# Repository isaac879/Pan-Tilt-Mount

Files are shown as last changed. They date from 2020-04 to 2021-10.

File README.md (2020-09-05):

# 3-Axis Slider
A stepper motor driven, 3D printed and Arduino Nano controlled 3-axis slider.

Project Overview:
This is the 3-axis slider I designed for my DSLR Canon EOS 250D (EOS Rebel SL3). I designed it for video motion control, time-lapses and panoramic shots.

Here is a quick overview of the components and how the project works. There is an Arduino Nano as the brain controlling everything and monitoring the inputs. The three Nima 17 stepper motors are controlled by TMC2208 stepper driver boards. When combining the stepper motor’s step angle, the microstepping mode of the driver boards and the gear ratios of the pan and tilt axis you get a precision of 0.0133° and 0.0369° respectively (Stepper motors move 1.8° per full step, microstepping divides this by 16, the pan axis has a gear ratio of 144:17 and the tilt has a ratio of 64:21). 
The slider carriage moves using a 36 tooth timing pulley with a 2GT timing belt on 2040 V-slot aluminium extrusion. This gives the slider has a positional precision of approximately 0.0225mm.

In 16th microstepping mode, axis speeds are limited to about 20 degrees per second for the pan, 15 degrees per second for the tilt and 20mm per second for the slider. This limit is due to the software/microcontroller speed which is only able to produce ~4000 step pulses per second for the 3 stepper motors. In half stepping mode speeds about eight times higher should be possible depending on acceleration profiles and camera weight.

The pan, tilt and slider are almost completely silent in 16th microstepping mode. In half stepping mode when moving at full speed the noise is audible.

The maximum weight I have tested it with is just over 1kg. This was with my Canon EOS 250D with the heaviest lens I have (Canon EF-S 18-135mm f/3.5-5.6) and a Rode Video Mic Pro+. This worked without any issues although some shaking does occur when rapidly changing directions.

There are Hall effect sensors and magnets embedded in the pan, tilt and slider axis to allow the stepper motors to home and zero themselves. The circuit can be powered by a 12V DC input or 3 cell LiPo battery for portability. With a 1000mAh battery the 3-axis slider can operate for abount one hour. The Arduino will monitors the battery level and print it out. The Arduino can also trigger the camera’s shutter using an NPN transistor and 2.5mm 3 pole jack. 

Communicating with the Arduino is simply over a serial connection provided by the USB or JDY-31 serial pass-through Bluetooth module.

The 3-Axis slider project video/demo: https://youtu.be/1FfB7cLkUyQ

Some picture, videos and development updates are available on my Instagram: https://www.instagram.com/isaac879/

The CAD STL and STEP files are available here: https://www.thingiverse.com/thing:4547074

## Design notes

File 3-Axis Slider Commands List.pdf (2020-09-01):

isaac879

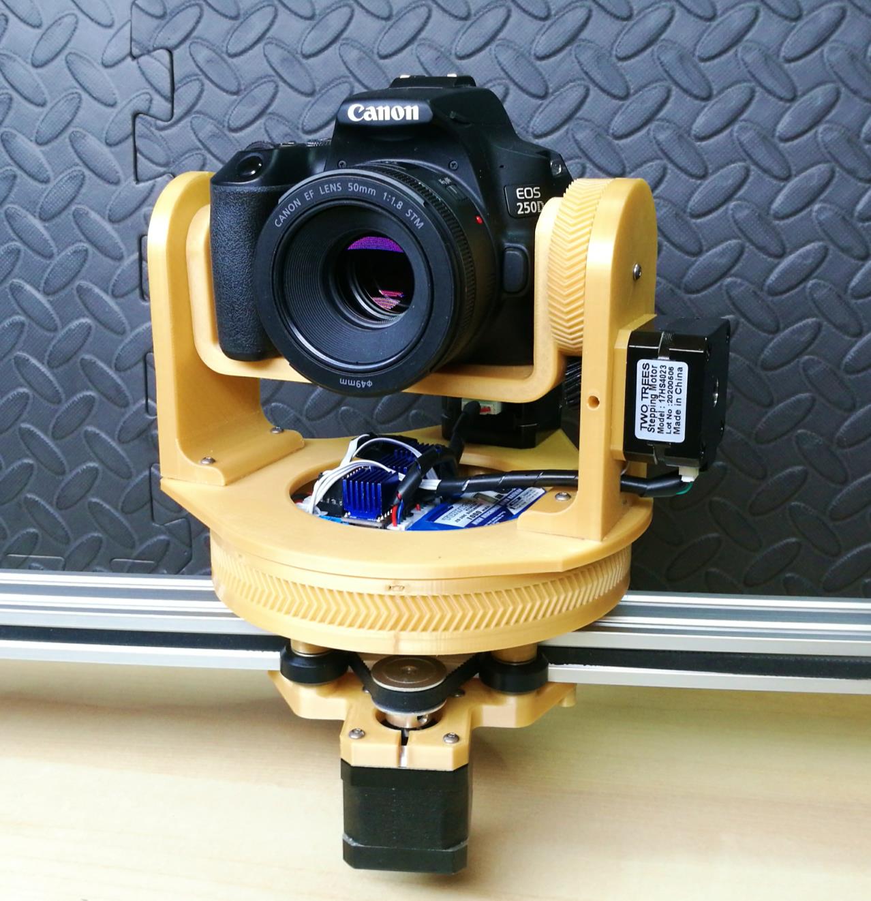
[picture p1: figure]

3-Axis Slider | Page 1 of 3

# 3-Axis Slider Commands List

Function | Command Character | Input Range
Report status | R | N/A
Set Step Mode | m | 2, 4, 8, 16
Pan x degrees | p | float
Tilt x degrees | t | float
Toggle enable motors | e | N/a
Set maximum pan speed (deg/s) | s | float
Set maximum tilt speed (deg/s) | S | float
Invert pan direction | i | bool
Invert tilt direction | I | bool
Set pan hall effect offset (deg) | o | float
Set tilt hall effect offset (deg) | O | float
Set homing mode (0: No homing, 1: Slider, 2: Pan & Tilt, 3: All axis) | H | 0-3
Trigger camera shutter | c | N/A
Auto home the axis | A | N/A
Execute moves array | ; | 1-32767
Add current position to moves array | # | N/A
Step forward a position in the moves array | > | N/A
Step backward a position in the moves array | < | N/A
Move to the first position in the moves array | [ | N/A
Move to the last position in the moves array | ] | N/A
Edit the current position in the moves array with current position | E | N/A
Add a delay in the moves array (ms) | d | 0-32767
Edit a delay at the current position in the moves array (ms) | D | 0-32767
Clear all position in the moves array | C | N/A
Save the current settings in EEPROM | U | N/A
Start a panoramic-lapse | L | N/A
Set angle between pictures (deg) | b | float
Set delay between pictures (ms) | B | 0-32767
Start a time lapse with x pictures | l | 1-32767
Move slider x mm | x | float
Invert slider direction | j | bool
Set maximum slider speed (mm/s) | X | float
Auto Home the slider axis | Z | N/A
Calculate the intercept of the first 2 keyframes | T | N/A
Move between the 2 keyframes, keeping pointed at the intercept | @ | 0-32767
Toggle axis acceleration on/off | a | N/A
Pan acceleration increment delay (µs) | q | 0-32767
Tilt acceleration increment delay (µs) | Q | 0-32767
Slider acceleration increment delay (µs) | w | 0-32767
Scale the speed of all keyframed movements | W | float

To use a function listed in the table you need to send the appropriate command over the serial connection to the Arduino. The serial connection can be over USB or Bluetooth as they both work the same. You can simply use the serial monitor provided in the Arduino IDE or one of many Android apps (I use Arduino Bluetooth controller by Giumig Apps). Bluetooth modules commonly have a default baud rate of 9600 which will need to be changed to 57600 to avoid any timing issues with the code.

Examples:
To get the pan tilt mount to print out its current status just send “R” (without quotes). To set the step mode to 16th stepping move send: “m16” (without quotes).
To move the pan axis -22.5 degrees send: “p-22.5” (without quotes).

Important:
When the code is first uploaded the EEPROM values will not have been properly set and will result in unusable values. You will need to set appropriate values then save them to the EEPROM (by sending he command character U). A restart may then be required.
To see the current setting and stored EEPROM values send the command character R. The screenshots below show the settings and stored values before and after setting appropriate EEPROM values.

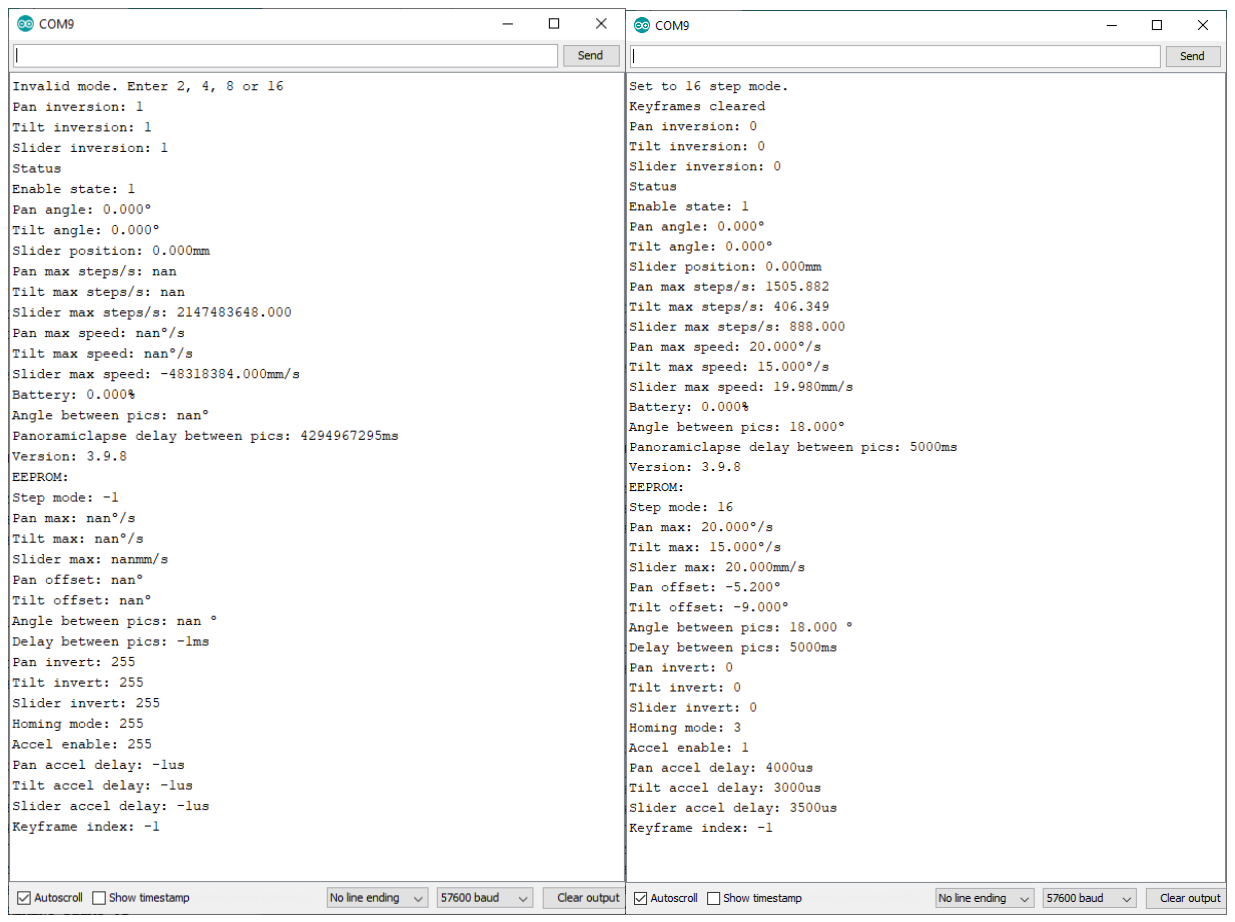
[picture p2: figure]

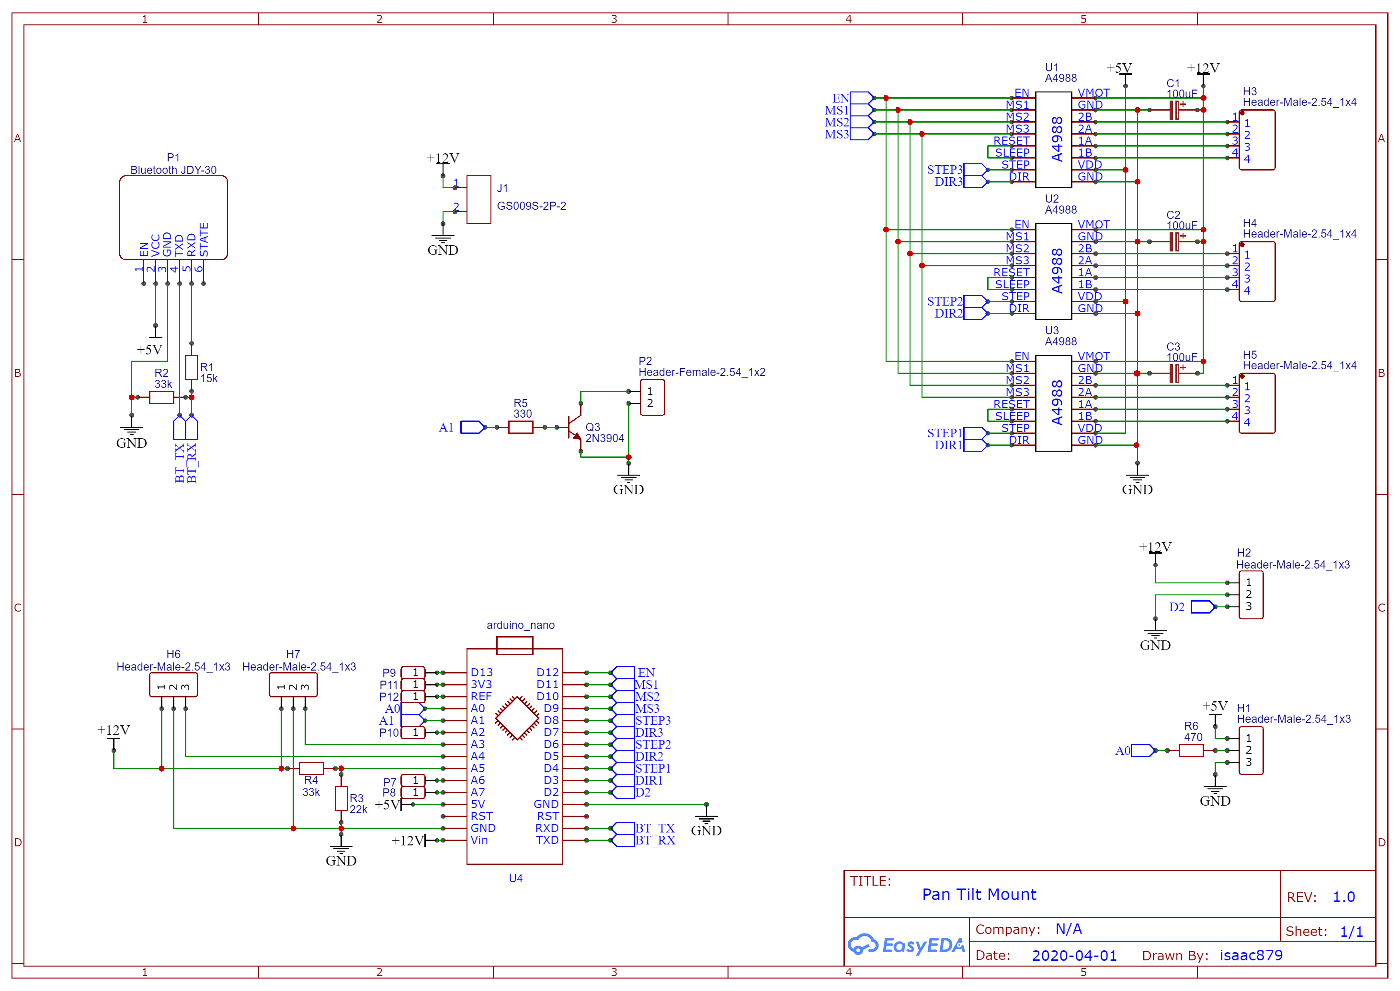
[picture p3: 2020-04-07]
Schematic_Pan Tilt Camera Mount_Sheet_1_20200401234411.png

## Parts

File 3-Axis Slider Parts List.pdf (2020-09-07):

isaac879

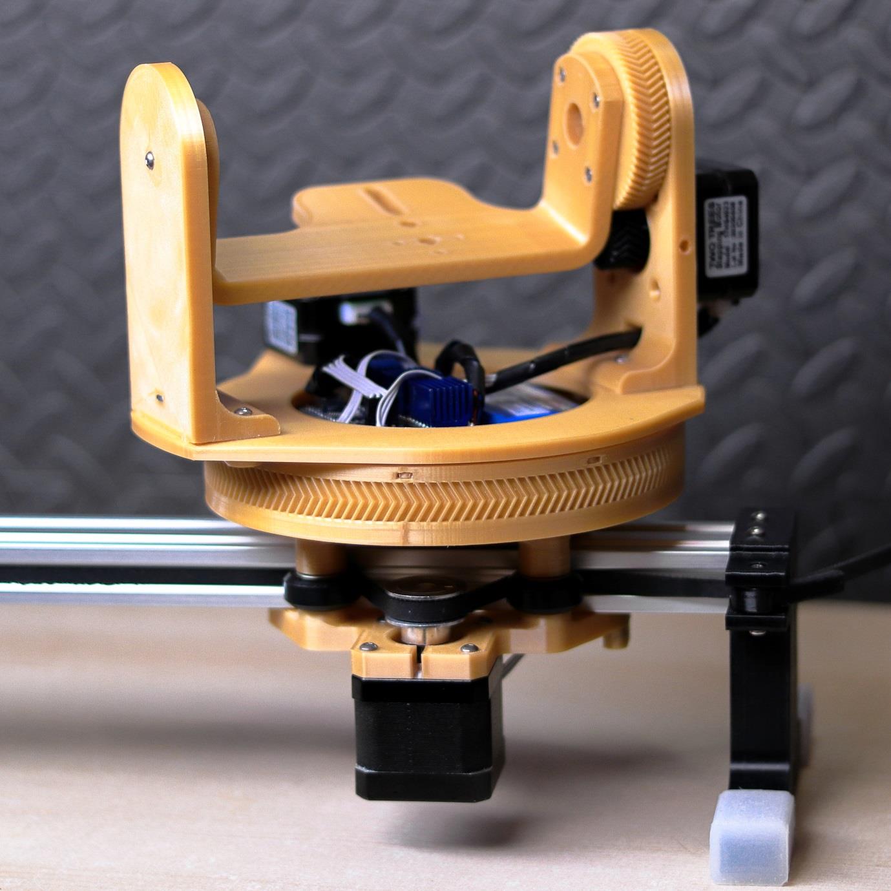
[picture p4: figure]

Linear Slider | Page 1 of 3

# 3-Axis Slider Parts List

3-Axis Slider Parts | Quantity
Nema 17 42 x 42 x 40mm Stepper Motor | 1
Nema 17 42 x 42 x 23mm Stepper Motor | 2
TMC2208 Stepper Motor Driver | 3
Arduino Nano | 1
JDY-31 Bluetooth Module (Alternatively HC-05, HC-06 or JDY-30) | 1
A3144 Hall Effect Sensor | 3
6.4mm diameter x 1.7mm Neodymium Magnets | 2
3.2mm diameter x 1.7mm Neodymium Magnets | 4
2N3904 NPN Transistor | 1
330Ω Resistor | 1
470Ω Resistor | 1
15kΩ Resistor | 1
22kΩ Resistor | 1
33kΩ Resistor | 2
100µF Electrolytic Capacitor | 3
2 Pin Plug-In Screw Terminal Block Connector 5.08mm Pitch (for power) | 1
6 Pin Female Header Connector 2.54mm (for Bluetooth module) | 1
15 Pin Female Header Connector 2.54mm (for Arduino Nano) | 2
15 Pin Male Header Connector 2.54mm (for Arduino Nano) | 2
8 Pin Female Header Connector 2.54mm (for Stepper drivers) | 6
8 Pin Male Header Connector 2.54mm (for Stepper drivers) | 6
XH2.54 4 Pin Terminal Socket Header (for Stepper motors) | 3
XH2.54 4 Pin Terminal Socket Plug (for Stepper motors) | 3
XH2.54 3 Pin Terminal Socket Header (for Hall Effect) | 3
XH2.54 3 Pin Terminal Socket Plug (for Hall Effect) | 3
XH2.54 2 Pin Terminal Socket Header (for camera shutter trigger) | 1
XH2.54 2 Pin Terminal Socket Plug (for camera shutter trigger) | 1
2.5mm 3 pole Jack Male (for camera trigger) | 1
11.1V 3S LiPo Battery or 12V DC Power Source and connector to screw terminal | 1
Pan Tilt Mount PCB | 1
Solder Wire
Cyanoacrylate or Hot Glue (for magnets and Hall Effect sensor) Wire (for Stepper motors, Hall sensors, Bluetooth module)
M3 Hexagonal Nyloc Nut | 16
M3 Square Nut | 10
M3 Button Head Hex Bolt 40mm | 4
M3 Button Head Hex Bolt 20mm | 3
M3 Button Head Hex Bolt 16mm | 10
M3 Button Head Hex Bolt 12mm | 14
M3 Button Head Hex Bolt 8mm | 5
M3 Button Head Hex Bolt 6mm | 5
M3 Button Head Hex Bolt 3.5mm | 1
Camera Mounting Bolt | 1
M3 T-Nut for Aluminium Extrusion Profile | 4

Screw 2mm Outer Thread Diameter, 6mm Long | 3
2GT Timing Belt | 1
2GT Timing Pulley 36 Teeth | 1
V-Slot 2040 Aluminium Extrusion | 1
F623ZZ Flange Bushing Ball Bearings 3 x 10 x 4mm | 6
V-Slot Pulley Wheels with Bearings (24 x 16 x 10.2mm) | 4
3D Printed Parts
127 x 146.05 x 12.7mm INA CSXU050-2RS Bearing Or 3D printable bearing parts 1-3 and 28 x 6mm balls (BB pellets) | 1
21 Tooth Herringbone Gear | 1
64 Tooth Herringbone Gear | 1
17 Tooth Herringbone Gear | 1
144 Tooth Herringbone Gear Base Mount | 1
Tilt U-Mount | 1
Idle Side Bearing Mount | 1
Gear Side Bearing Mount | 1
Idle Side Support | 1
Gear Side Support | 1
Pan Mount | 1
Pan Mount Bearing Clamp | 1
Base Mount Bearing Clip Ring | 1
2040 hall clamp | 1
2040 slider carriage top | 1
2040 slider carriage bottom | 1
2040 belt clamp side 1 | 1
2040 belt clamp side 2 | 1
2040 support leg (Optional)
Belt clamp lever | 2
3mm to 5mm wheel bearing spacer centred | 4
5mm to 8mm shaft spacer (for timing pulley if it has a 8mm bore) | 1

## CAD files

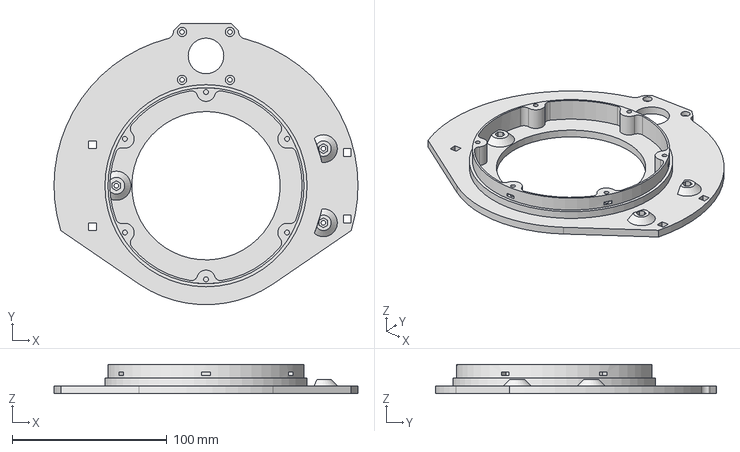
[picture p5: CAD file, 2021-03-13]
3-Axis Slider CAD STEP Exports/Pan Mount.stp
196.7 x 181.9 x 18.8 mm

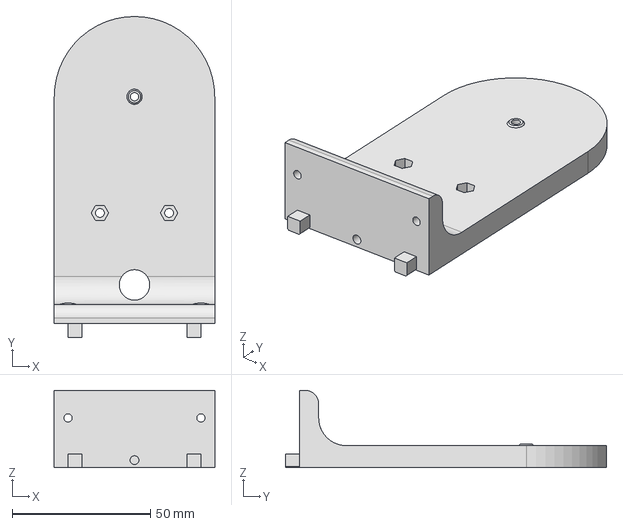
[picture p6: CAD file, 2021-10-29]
LP-E6 Battery Mount/Idle Side Support.stp
58.0 x 116.0 x 28.0 mm

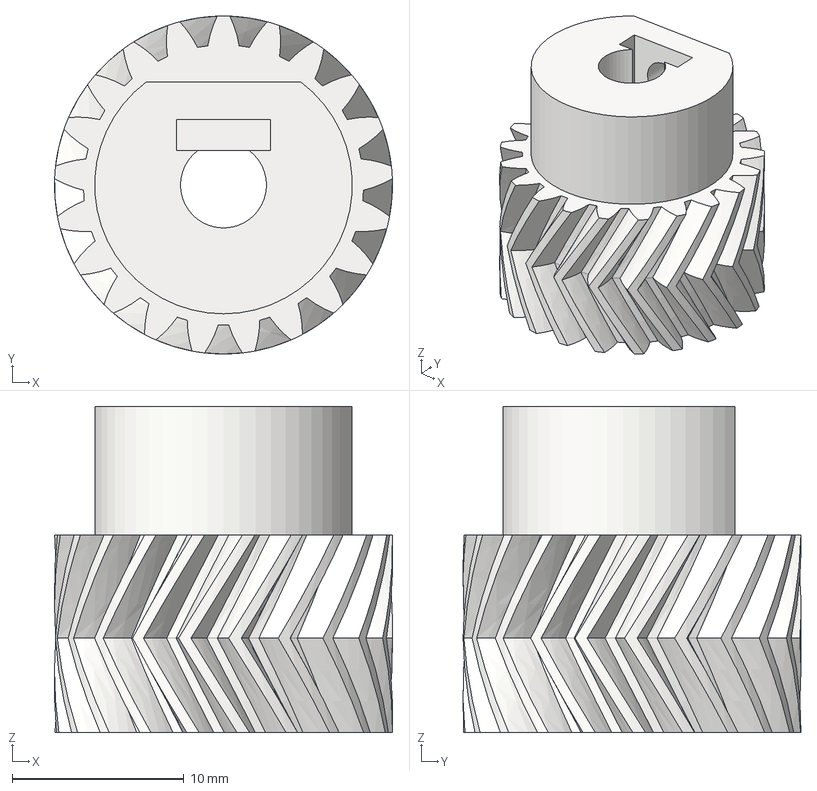
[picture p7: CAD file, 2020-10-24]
3-Axis Slider CAD STEP Exports/21 Tooth Herringbone Gear.stp
19.7 x 19.7 x 19.0 mm

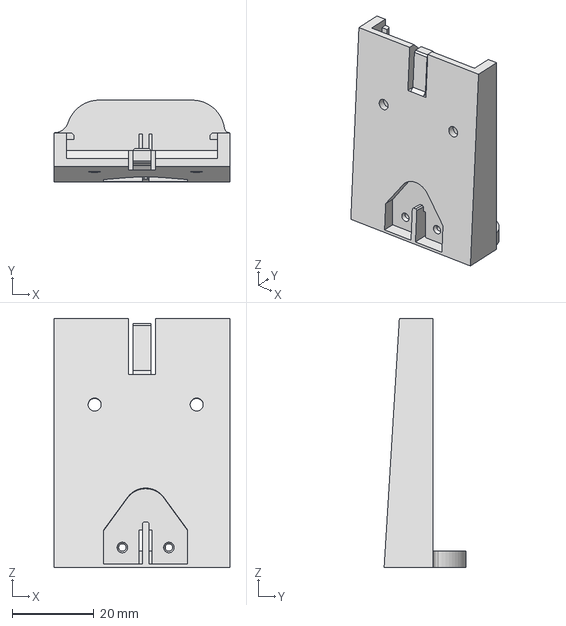
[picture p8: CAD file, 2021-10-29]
LP-E6 Battery Mount/LP-E6 Battery Holder Mount.stp
43.0 x 20.0 x 61.0 mm

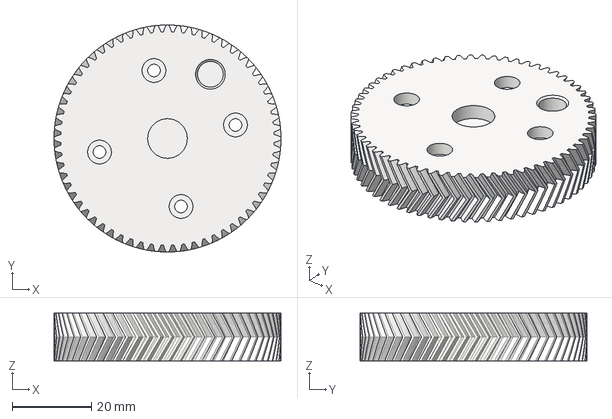
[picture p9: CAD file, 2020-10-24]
3-Axis Slider CAD STEP Exports/64 Tooth Herringbone Gear.stp
57.3 x 57.3 x 12.0 mm

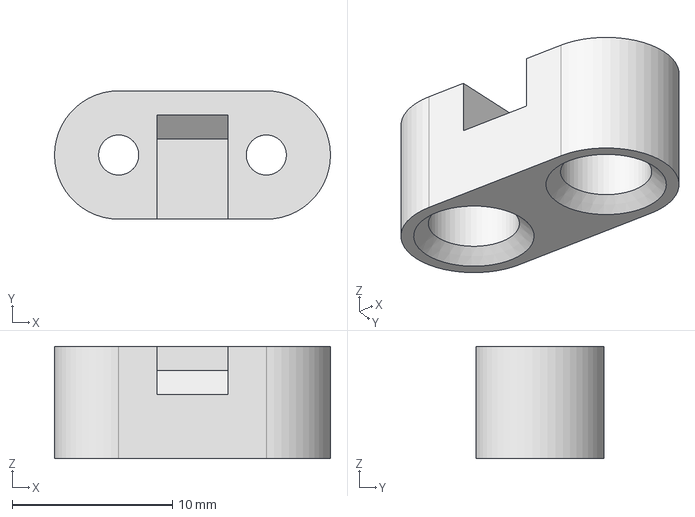
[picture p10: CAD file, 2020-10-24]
3-Axis Slider CAD STEP Exports/2040 hall clamp.stp
17.2 x 8.00 x 7.00 mm

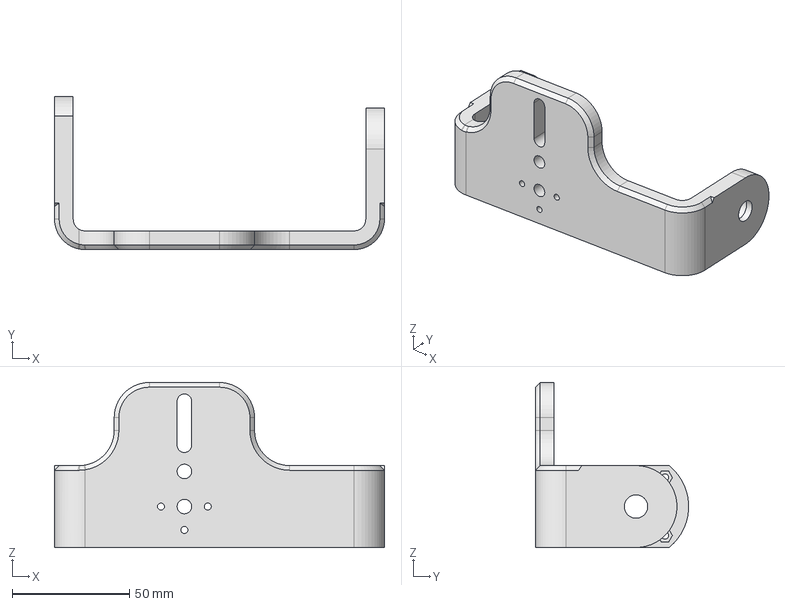
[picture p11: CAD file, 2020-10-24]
3-Axis Slider CAD STEP Exports/Tilt U-Mount.stp
141.0 x 65.5 x 70.5 mm

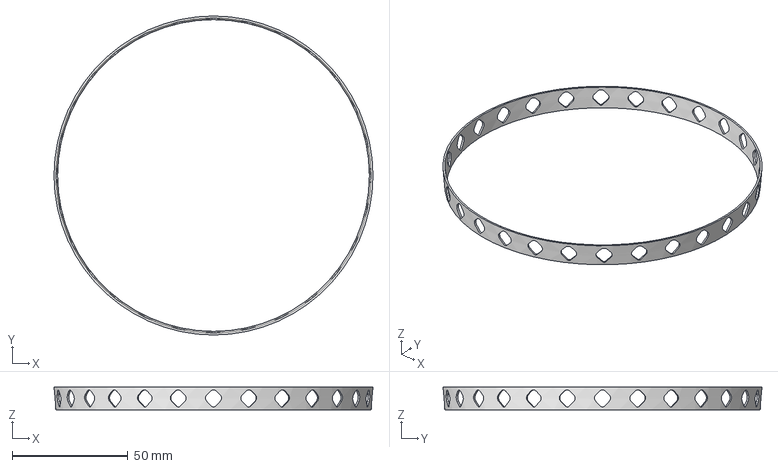
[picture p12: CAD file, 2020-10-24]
3-Axis Slider CAD STEP Exports/127 x 146.05 x 12.7mm Printable Bearing Cage Part 3.stp
138.1 x 138.1 x 9.90 mm

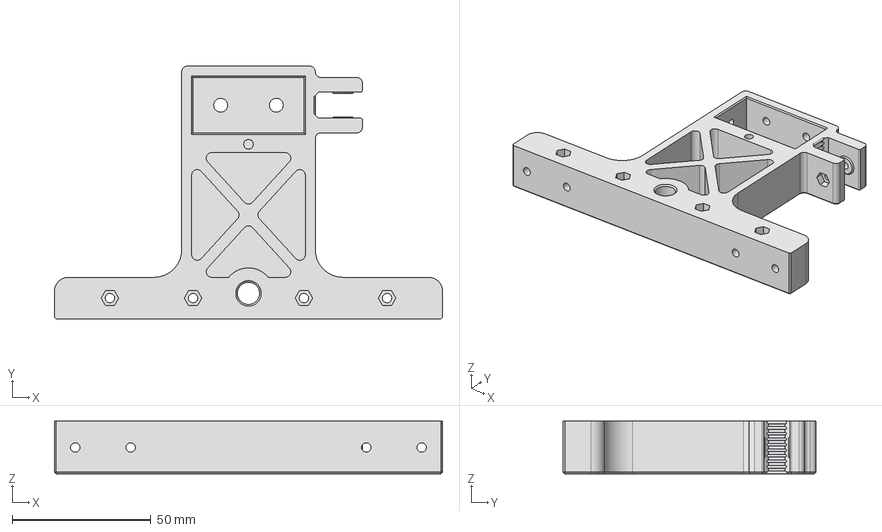
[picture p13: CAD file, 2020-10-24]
3-Axis Slider CAD STEP Exports/2040 belt clamp side 1.stp
140.0 x 91.2 x 19.0 mm

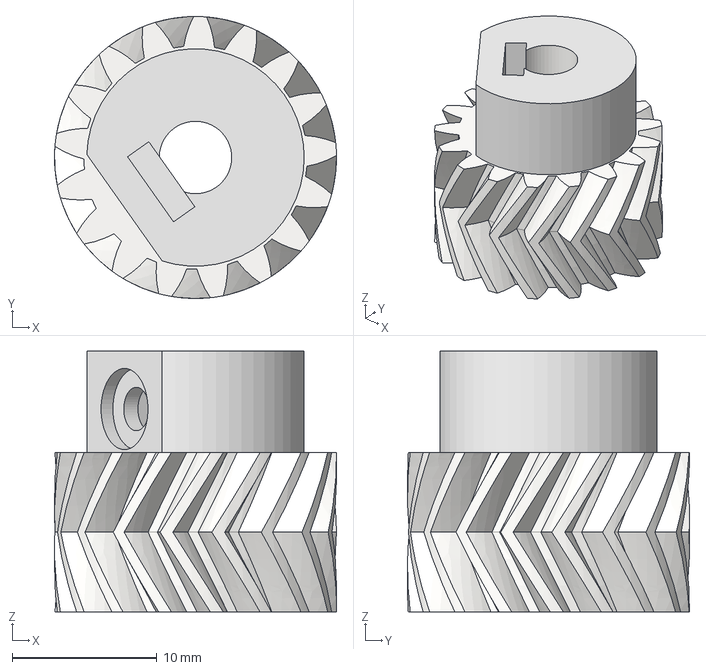
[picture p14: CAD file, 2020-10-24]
3-Axis Slider CAD STEP Exports/17 Tooth Herringbone Gear.stp
19.5 x 19.5 x 18.0 mm

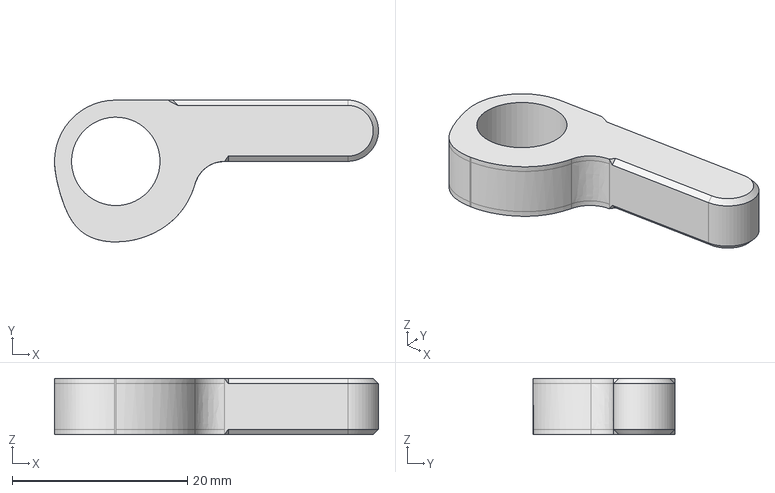
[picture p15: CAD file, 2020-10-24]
3-Axis Slider CAD STEP Exports/belt clamp lever.stp
37.0 x 16.2 x 6.40 mm

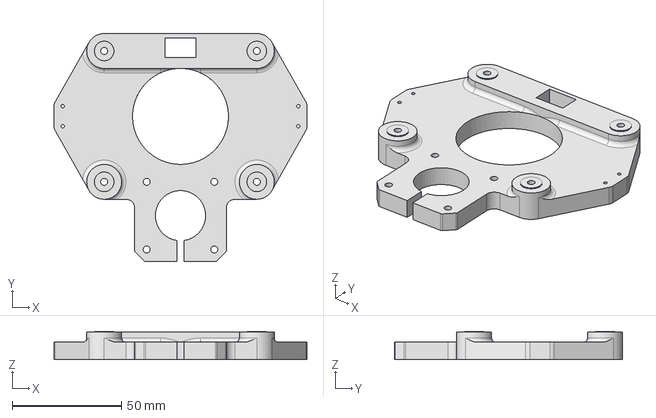
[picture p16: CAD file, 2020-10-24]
3-Axis Slider CAD STEP Exports/2040 slider carriage bottom.stp
116.0 x 104.5 x 13.0 mm

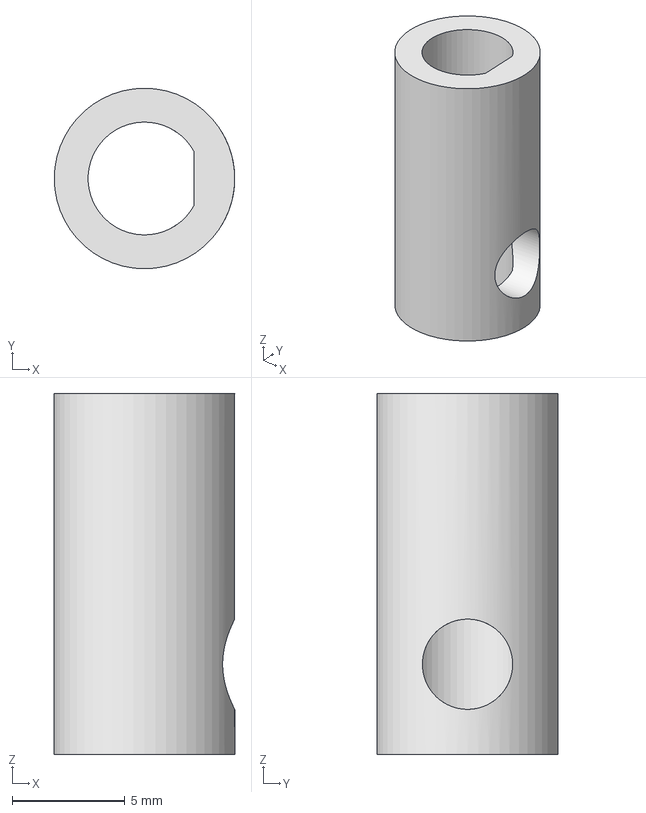
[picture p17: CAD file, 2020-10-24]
3-Axis Slider CAD STEP Exports/5mm to 8mm shaft spacer.stp
8.00 x 8.00 x 16.0 mm

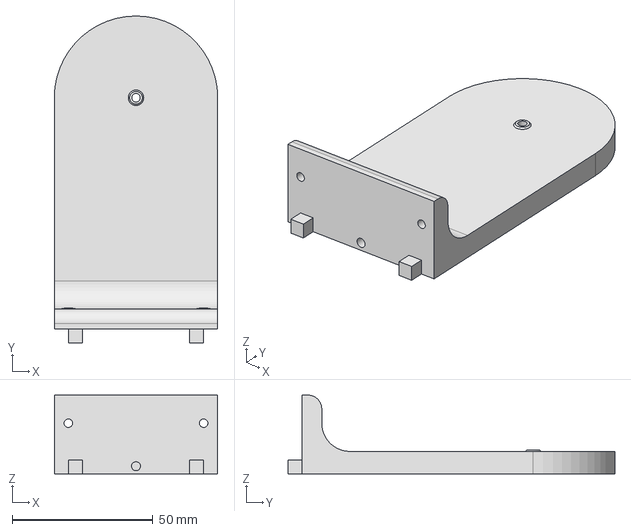
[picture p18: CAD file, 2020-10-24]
3-Axis Slider CAD STEP Exports/Idle Side Support.stp
58.0 x 116.0 x 28.0 mm

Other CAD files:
3-Axis Slider CAD STEP Exports/Base Mount Bearing Clip Ring.stp
3-Axis Slider CAD STEP Exports/2040 belt clamp side 2.stp
3-Axis Slider CAD STEP Exports/Hall Effect Stepper Mount.stp
3-Axis Slider CAD STEP Exports/127 x 146.05 x 12.7mm Printable Bearing Part 1.stp
3-Axis Slider CAD STEP Exports/127 x 146.05 x 12.7mm Printable Bearing Part 2.stp
3-Axis Slider CAD STEP Exports/144 Tooth Herringbone Gear Base Mount.stp
3-Axis Slider CAD STEP Exports/17 Tooth Herringbone Gear Flexi.stp
3-Axis Slider CAD STEP Exports/2040 slider carriage top.stp
3-Axis Slider CAD STEP Exports/2040 support leg.stp
3-Axis Slider CAD STEP Exports/21 Tooth Herringbone Gear Flexi.stp
3-Axis Slider CAD STEP Exports/3mm to 5mm wheel bearing spacer centred.stp
3-Axis Slider CAD STEP Exports/Gear Side Support.stp
3-Axis Slider CAD STEP Exports/Pan Mount Bearing Clamp.stp
LP-E6 Battery Mount/Idle Side Support.stl
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

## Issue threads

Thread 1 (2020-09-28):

Sourcing parts

TaylorHokanson, 2020-09-28:
Hi Isaac! I'm planning on building one of these, but I'm having trouble with some of the part specifications. Could you be more descriptive about the motors, for example? Are they uni/bi-polar, what is the torque value, etc.? I'm also curious to hear about which suppliers you used, as Digikey (I'm in the states) doesn't recognize the Bluetooth module part number among others. How long should the belts be? Thanks!

MrScottFletcher, 2020-12-23:
Amazon.com had all of the parts in December 2020.  Check the "3-Axis Slider Parts List.pdf" for part numbers.

jonowelser, 2020-12-28:
I've also been hitting speedbumps in the process of sourcing parts, and I can see descriptions/dimensions but not specific part numbers in the "3-Axis Slider Parts List.pdf".

This may help with the motors:

- **For the 42 x 42 x 23mm stepper motors**: I was able to see the motor data tag [at 2:30 in this video](https://youtu.be/1FfB7cLkUyQ), and it looks like the manufacturer is "Two Trees" and the model is "17HS4023". If so, the exact motor [may be on Amazon here](https://www.amazon.com/Twotrees-Nema-17-Stepper-Motor/dp/B07ZVLYL25).
- **For the 42 mm x 42 mm x 40 mm stepper motor**: Its harder to see the tag in the clip above, but the part number may be "SL42STH40-1684A" (no manufacturer visible). If so, [here are motors specs](https://3dprint.wiki/reprap/anet/a8/steppermotor) and the manufacturer may be Guangzhou Shenglong Motor Co., Ltd - I can't find the exact model on their AliBaba page, but found two other listings on AliExpress for this part number which can be found [here](https://www.aliexpress.com/item/32842920299.html) and [here](https://www.aliexpress.com/item/32722953463.html). I'll probably source a motor with the same specs from somewhere else ([possibly like this](https://www.amazon.com/DROK-2-Phrase-Universal-Electric-Engraving/dp/B06XSYP24P/)).

Here where I'm stuck: What is a stepper motor driver I can use?

- **Assuming TMC2208 is correct (see below)**: Does the "version" matter? Ex: [this listing](https://www.amazon.com/Printer-TMC2208-Screwdriver-Controller-Ramps1-4/dp/B082LSQWZF) on Amazon is for TMC2208 V1.2, but [this one](https://www.amazon.com/BIGTREETECH-TMC2208-Stepper-Driver-Printer/dp/B07WGCF3L2) is for TMC2208 V3.0 - does that matter at all? Also, that second listing also has different models for STEP and UART modes; which mode would likely be better?
- **TMC2208 vs A4988**: I noticed that parts list describes the stepper motor drivers as part number TMC2208, but the wiring diagram ("Schematic_Pan Tilt Camera Mount_Sheet_1_20200401234411.png") lists them as A4988, which is also what they look like in [this video](https://www.youtube.com/watch?v=uJO7mv4-0PY) from May 2020. They mostly* seem to have the same pinouts, but the TMC2208's seem to have taller heatsinks than the A4988's, although I haven't gotten far enough to see if that's an issue (I just know the final assembly is nice and snug).
  - *While searching, I think I saw a couple TMC2208's and/or A4988's that had the outputs 1A / 1B / 2A / 2B  in a different order than on the schematic / other manufacturers on the market (just make sure the order is 2B / 2A / 1A / 1B like the schematic, reading from top to bottom).

PS I just want to say this whole project is absolutely incredible. The level of quality and attention to detail in everything from the the 3d files, code, YouTube videos, and documentation in this repository are amazing - this is one of the best 3d printing/electronics projects I've ever seen shared, and I can't wait until I'm done building it!

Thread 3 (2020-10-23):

WiFi Control

PastuDan, 2020-10-23:
Really incredible project @isaac879!

I started on something similar a while back, but single-axis only. My goal was to take sharper time-lapses by getting the microcontroller to move the steppers, and then trigger a timelapse photo on the camera after movement had fully stopped. I was using an esp8266, so I was trying to reverse engineer the Canon WiFi protocol to be able to trigger the shutter from the microcontroller without wires. I successfully triggered the shutter using some JavaScript code, but never got it ported: https://github.com/PastuDan/ptpip-test/blob/master/test.js#L114-L115

Let me know if you're interested, and I can explain in a little more detail how I came up with those shutter codes... It's actually not too complicated! I was using the Canon iPhone app with WireShark (which understands the [picture transfer protocol](https://www.wireshark.org/docs/dfref/p/ptpip.html)) to capture the network requests, ie the `1a000000060000000100000028919a0100000300000001000000` sequence that's hardcoded in my js code, and then replaying that over the network socket to the camera's IP.

Congrats again on the hardware. Your 3d printed parts turned out far more professional than my metalworking :-p Here's my embarassing [youtube video](https://www.youtube.com/watch?v=8tqtJsu3-bM&t=215s) if you're curious.

botio, 2020-11-18:
grbl-esp32. https://github.com/bdring/Grbl_Esp32/tree/main/Grbl_Esp32/src/Machines
there are lots of machine types, one of them is only with 2axises with small board design.

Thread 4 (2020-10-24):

STP sources for several STL files are missing on Thingiverse

Bougakov, 2020-10-24:
Hi. I think the slider carriage files are missing from the archive with the STP sources. Could you please upload all the files here? STP files are ASCII-based, so GitHub is a perfect place for them.

Bougakov, 2020-10-24:
Oh, I sorted this out - the slider carriage files were in the earlier iteration. Created a PR that mentions it in README

Bougakov, 2020-10-24:
Oops, no. Those older files are for 2020 profile; STP files for 2040 are nowhere to be found :((

isaac879, 2020-10-24:
I've just added all the STEP files to the GitHub repository. I think there might have been some issue with thingiverse because someone else was also missing a files but when I check the zip folder I uploaded they were all in there... Not really sure what caused it but anyway the files are here now too.

Bougakov, 2020-10-24:
Thanks. I have two parallel 2020 bars (they can be assembled in 20*80, or 20*100 basically using shorter cuts); I will try to figure out how to tinker with the carriage to make the distance between wheels larger so it would fit my rails:

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

dronecz, 2021-03-07:
Hi, as I´m doing some modifications to you design, I download you GH files and there is STEP file missing for "Pan Mount" file. There is one in STL format, but that is terrible format for editing. Can you @isaac879  pls upload it?

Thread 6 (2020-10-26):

Loop a movement?

dr00pyd, 2020-10-26:
Hi, When you put the cameras on a keyframe and it continues to follow that object, can you make it loop and go back and forth until you choose to stop? I would like to use your project for my live stream so can can get a paralaxefect. Anyway I really like the project and so you can order pcbn, so I have done it now.

thanks so much.

isaac879, 2020-11-03:
You can set the number of times for it to repeat a movement but unfortunately there currently isn't a way to stop it half way through.

Closed 2020-11-03.

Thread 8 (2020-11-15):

is it possible to use grbl with this pcb board? so we can use gcode to control it too?

botio, 2020-11-15:
is it possible to use grbl with this pcb board? so can use gcode to control it too?

like I said, I did try burn grbl on the arduino Nano with this pcb, so can use gcode to script some movement.

but I have some trouble for the pin setting up for grbl.... hope someone can try it and figure it out

botio, 2020-11-18:
okay, it does work. close and go to find out wifi solution.

Closed 2020-11-18.

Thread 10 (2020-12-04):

wich balls for the self printing bearing

goldjunge91, 2020-12-04:
Hi
wich balls i need to buy for the bearing and why you not use a normal bearing

saikosys, 2020-12-04:
they're standard 6mm plastic BBs.

A bearing of that size would be very expensive.

goldjunge91, 2020-12-04:
yeah thanks i have see it now.

Closed 2020-12-04.

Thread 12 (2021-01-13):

Scale joystick input to maxSpeed

cbradburne, 2021-01-13:
Currently the joystick sets the motor speed directly (-255 , 255) which moves the axis quite slowly. May I suggest scaling the joystick input to the set maxSpeed?

At line 985 of panTiltMount.cpp:
`sliderStepSpeed = (sliderStepSpeed * (stepper_slider.maxSpeed() / 255));`
`panStepSpeed = (panStepSpeed * (stepper_pan.maxSpeed() / 255));`
`tiltStepSpeed = (tiltStepSpeed * (stepper_tilt.maxSpeed() / 255));`

I'd issue a pull request but I'm not 100% on how to do that correctly! :)

Closed 2021-03-15.

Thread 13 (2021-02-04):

shematic

hyperion11, 2021-02-04:
hello! in what program made schematic for control board?
i wish to modify it.
Can you add it to github?
For my camera i need two wires  - shutter control and focus control. Without "clicking" focus it not release shutter (Sony A7S)
Thanks!

Glivmo, 2021-02-04:
You can find the schematic and pcb design on easyeda and use the web editor to edit it:
https://easyeda.com/isaac879/pan-tilt-camera-mount_copy

Closed 2021-02-04.

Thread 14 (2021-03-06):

3D printer board as "Mainboard"

sibero80, 2021-03-06:
Given that most 3D printer boards work with an ATmega processor.. could it be possible to use one of those boards as the base of this project with minor modifications to the code?

dronecz, 2021-03-07:
Yes, it should be no problem to drive stepper motors with it. There will probably be small issue with sensing of voltage in battery and with controlling your shutter at camera, but that will depend what 3D printer controller you will use and how good you are with modifications of HW 😉

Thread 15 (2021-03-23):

Stuttering and slight pausing.

killrmodz, 2021-03-23:
I have everything up and running.  The only issue i'm having are two fold.  Based on the video, I cannot get my velocity to be the same.  Also, there are momentary pauses and stutters in manual movement and sometime in the movement arrays.  I'm not sure where to start.  Any ideas?

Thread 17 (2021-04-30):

Bluetooth Communication

przemo, 2021-04-30:
Hi,
I am not experienced in programming arduino, but can you explain how the BT serial can be enabled?

Thanks!

JakobWalk, 2021-05-04:
If you connect your BT module according to the description it should be enabled by default.
It's important that you use the same baud rate on the arduino and the BT module.
You can change the baud rate of your BT module by connecting it via serial to your pc and use AT commands to configure it.

przemo, 2021-05-14:
Ahh, thanks for explanation. Probably , the baud rate, is not set up properly. Thanks.

przemo, 2022-09-12:
Resolved by changing baud rate

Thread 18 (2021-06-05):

Changing step motor driving pins

vshamsiv, 2021-06-05:
Hi, thank you for your perfect project. As making the PCB is hard and in the meantime CNC shied available; is it possible to modify your code as below the we can use that shield :
(I copied this from grbl library in cpu_mapnn.h).
// Define step pulse output pins. NOTE: All step bit pins must be on the same port.
#define STEP_DDR        DDRD
#define STEP_PORT       PORTD
#define X_STEP_BIT      3 // Uno Digital Pin 2
#define Y_STEP_BIT      5  // Uno Digital Pin 3
#define Z_STEP_BIT      7  // Uno Digital Pin 4
#define STEP_MASK       ((1<<X_STEP_BIT)|(1<<Y_STEP_BIT)|(1<<Z_STEP_BIT)) // All step bits

// Define step direction output pins. NOTE: All direction pins must be on the same port.
#define DIRECTION_DDR     DDRD
#define DIRECTION_PORT    PORTD
#define X_DIRECTION_BIT   2  // Uno Digital Pin 5
#define Y_DIRECTION_BIT   4  // Uno Digital Pin 6
#define Z_DIRECTION_BIT   6  // Uno Digital Pin 7
#define DIRECTION_MASK    ((1<<X_DIRECTION_BIT)|(1<<Y_DIRECTION_BIT)|(1<<Z_DIRECTION_BIT)) // All direction bits

// Define stepper driver enable/disable output pin.
#define STEPPERS_DISABLE_DDR    DDRB
#define STEPPERS_DISABLE_PORT   PORTB
#define STEPPERS_DISABLE_BIT    8  // no Digital Pin 8
#define STEPPERS_DISABLE_MASK   (1<<STEPPERS_DISABLE_BIT)

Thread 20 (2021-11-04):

Pinout

Cysign, 2021-11-04:
Hi,
I'm not sure what to connect to the different pinheaders.
Is there a building tutorial (like on instructables)?

H1, H2, H6, H7, P2 are not clear for me.
H should be the hall sensors. But which one belongs to which place?
And what's P2 good for? Is it the camera trigger?

jkowalk, 2021-11-05:
Have you had a look at the Schematic_Pan Tilt Camera Mount_Sheet_1_20200401234411.png. Also there are Videos on the YouTube channel isaac879. Also you can check the Arduino code to see which pins are used for what.

H2, H6 and H7 are connected to the hall sensors.
H1, I think, is not used in the current version without a programmable led.
And P2 is for the trigger.

I hope that helps.

Cysign, 2021-11-05:
That's why I'm asking. There's no information about the connected components for the P2, H1, H2...
I didn't have a look at the code yet, as I'm still printing parts ;)
Youtubevideos are never a good reference for schematics... they might explain steps for beginners....but I prefer the traditional way with pictures, legends and schematics.
At least most of the videos about electronics don't contain any information about revisions and pinouts...

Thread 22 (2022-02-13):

Issues with compiling

Bobsblobblog, 2022-02-13:
Giving you the verbose logging.  I am just not used to troubleshooting these compiling issues.

Arduino: 1.8.19 (Mac OS X), Board: "Arduino Nano, ATmega328P"

/private/var/folders/y8/0kkt82m53ys2jryw13_s1tgw0000gn/T/AppTranslocation/272F7157-364F-421C-AACB-7350368DEA12/d/Arduino.app/Contents/Java/arduino-builder -dump-prefs -logger=machine -hardware /private/var/folders/y8/0kkt82m53ys2jryw13_s1tgw0000gn/T/AppTranslocation/272F7157-364F-421C-AACB-7350368DEA12/d/Arduino.app/Contents/Java/hardware -tools /private/var/folders/y8/0kkt82m53ys2jryw13_s1tgw0000gn/T/AppTranslocation/272F7157-364F-421C-AACB-7350368DEA12/d/Arduino.app/Contents/Java/tools-builder -tools /private/var/folders/y8/0kkt82m53ys2jryw13_s1tgw0000gn/T/AppTranslocation/272F7157-364F-421C-AACB-7350368DEA12/d/Arduino.app/Contents/Java/hardware/tools/avr -built-in-libraries /private/var/folders/y8/0kkt82m53ys2jryw13_s1tgw0000gn/T/AppTranslocation/272F7157-364F-421C-AACB-7350368DEA12/d/Arduino.app/Contents/Java/libraries -libraries /Users/benmatthews/Documents/Arduino/libraries -fqbn=arduino:avr:nano:cpu=atmega328 -ide-version=10819 -build-path /var/folders/y8/0kkt82m53ys2jryw13_s1tgw0000gn/T/arduino_build_541564 -warnings=none -build-cache /var/folders/y8/0kkt82m53ys2jryw13_s1tgw0000gn/T/arduino_cache_267269 -prefs=build.warn_data_percentage=75 -prefs=runtime.tools.avrdude.path=/private/var/folders/y8/0kkt82m53ys2jryw13_s1tgw0000gn/T/AppTranslocation/272F7157-364F-421C-AACB-7350368DEA12/d/Arduino.app/Contents/Java/hardware/tools/avr -prefs=runtime.tools.avrdude-6.3.0-arduino17.path=/private/var/folders/y8/0kkt82m53ys2jryw13_s1tgw0000gn/T/AppTranslocation/272F7157-364F-421C-AACB-7350368DEA12/d/Arduino.app/Contents/Java/hardware/tools/avr -prefs=runtime.tools.avr-gcc.path=/private/var/folders/y8/0kkt82m53ys2jryw13_s1tgw0000gn/T/AppTranslocation/272F7157-364F-421C-AACB-7350368DEA12/d/Arduino.app/Contents/Java/hardware/tools/avr -prefs=runtime.tools.avr-gcc-7.3.0-atmel3.6.1-arduino7.path=/private/var/folders/y8/0kkt82m53ys2jryw13_s1tgw0000gn/T/AppTranslocation/272F7157-364F-421C-AACB-7350368DEA12/d/Arduino.app/Contents/Java/hardware/tools/avr -prefs=runtime.tools.arduinoOTA.path=/private/var/folders/y8/0kkt82m53ys2jryw13_s1tgw0000gn/T/AppTranslocation/272F7157-364F-421C-AACB-7350368DEA12/d/Arduino.app/Contents/Java/hardware/tools/avr -prefs=runtime.tools.arduinoOTA-1.3.0.path=/private/var/folders/y8/0kkt82m53ys2jryw13_s1tgw0000gn/T/AppTranslocation/272F7157-364F-421C-AACB-7350368DEA12/d/Arduino.app/Contents/Java/hardware/tools/avr -verbose /Users/benmatthews/Downloads/Pan-Tilt-Mount-TMC2208-Drivers/pan_tilt_mount_nano_code_tmc2208/pan_tilt_mount_nano_code_tmc2208.ino
/private/var/folders/y8/0kkt82m53ys2jryw13_s1tgw0000gn/T/AppTranslocation/272F7157-364F-421C-AACB-7350368DEA12/d/Arduino.app/Contents/Java/arduino-builder -compile -logger=machine -hardware /private/var/folders/y8/0kkt82m53ys2jryw13_s1tgw0000gn/T/AppTranslocation/272F7157-364F-421C-AACB-7350368DEA12/d/Arduino.app/Contents/Java/hardware -tools /private/var/folders/y8/0kkt82m53ys2jryw13_s1tgw0000gn/T/AppTranslocation/272F7157-364F-421C-AACB-7350368DEA12/d/Arduino.app/Contents/Java/tools-builder -tools /private/var/folders/y8/0kkt82m53ys2jryw13_s1tgw0000gn/T/AppTranslocation/272F7157-364F-421C-AACB-7350368DEA12/d/Arduino.app/Contents/Java/hardware/tools/avr -built-in-libraries /private/var/folders/y8/0kkt82m53ys2jryw13_s1tgw0000gn/T/AppTranslocation/272F7157-364F-421C-AACB-7350368DEA12/d/Arduino.app/Contents/Java/libraries -libraries /Users/benmatthews/Documents/Arduino/libraries -fqbn=arduino:avr:nano:cpu=atmega328 -ide-version=10819 -build-path /var/folders/y8/0kkt82m53ys2jryw13_s1tgw0000gn/T/arduino_build_541564 -warnings=none -build-cache /var/folders/y8/0kkt82m53ys2jryw13_s1tgw0000gn/T/arduino_cache_267269 -prefs=build.warn_data_percentage=75 -prefs=runtime.tools.avrdude.path=/private/var/folders/y8/0kkt82m53ys2jryw13_s1tgw0000gn/T/AppTranslocation/272F7157-364F-421C-AACB-7350368DEA12/d/Arduino.app/Contents/Java/hardware/tools/avr -prefs=runtime.tools.avrdude-6.3.0-arduino17.path=/private/var/folders/y8/0kkt82m53ys2jryw13_s1tgw0000gn/T/AppTranslocation/272F7157-364F-421C-AACB-7350368DEA12/d/Arduino.app/Contents/Java/hardware/tools/avr -prefs=runtime.tools.avr-gcc.path=/private/var/folders/y8/0kkt82m53ys2jryw13_s1tgw0000gn/T/AppTranslocation/272F7157-364F-421C-AACB-7350368DEA12/d/Arduino.app/Contents/Java/hardware/tools/avr -prefs=runtime.tools.avr-gcc-7.3.0-atmel3.6.1-arduino7.path=/private/var/folders/y8/0kkt82m53ys2jryw13_s1tgw0000gn/T/AppTranslocation/272F7157-364F-421C-AACB-7350368DEA12/d/Arduino.app/Contents/Java/hardware/tools/avr -prefs=runtime.tools.arduinoOTA.path=/private/var/folders/y8/0kkt82m53ys2jryw13_s1tgw0000gn/T/AppTranslocation/272F7157-364F-421C-AACB-7350368DEA12/d/Arduino.app/Contents/Java/hardware/tools/avr -prefs=runtime.tools.arduinoOTA-1.3.0.path=/private/var/folders/y8/0kkt82m53ys2jryw13_s1tgw0000gn/T/AppTranslocation/272F7157-364F-421C-AACB-7350368DEA12/d/Arduino.app/Contents/Java/hardware/tools/avr -verbose /Users/benmatthews/Downloads/Pan-Tilt-Mount-TMC2208-Drivers/pan_tilt_mount_nano_code_tmc2208/pan_tilt_mount_nano_code_tmc2208.ino
Using board 'nano' from platform in folder: /private/var/folders/y8/0kkt82m53ys2jryw13_s1tgw0000gn/T/AppTranslocation/272F7157-364F-421C-AACB-7350368DEA12/d/Arduino.app/Contents/Java/hardware/arduino/avr
Using core 'arduino' from platform in folder: /private/var/folders/y8/0kkt82m53ys2jryw13_s1tgw0000gn/T/AppTranslocation/272F7157-364F-421C-AACB-7350368DEA12/d/Arduino.app/Contents/Java/hardware/arduino/avr
Detecting libraries used...
/private/var/folders/y8/0kkt82m53ys2jryw13_s1tgw0000gn/T/AppTranslocation/272F7157-364F-421C-AACB-7350368DEA12/d/Arduino.app/Contents/Java/hardware/tools/avr/bin/avr-g++ -c -g -Os -w -std=gnu++11 -fpermissive -fno-exceptions -ffunction-sections -fdata-sections -fno-threadsafe-statics -Wno-error=narrowing -flto -w -x c++ -E -CC -mmcu=atmega328p -DF_CPU=16000000L -DARDUINO=10819 -DARDUINO_AVR_NANO -DARDUINO_ARCH_AVR -I/private/var/folders/y8/0kkt82m53ys2jryw13_s1tgw0000gn/T/AppTranslocation/272F7157-364F-421C-AACB-7350368DEA12/d/Arduino.app/Contents/Java/hardware/arduino/avr/cores/arduino -I/private/var/folders/y8/0kkt82m53ys2jryw13_s1tgw0000gn/T/AppTranslocation/272F7157-364F-421C-AACB-7350368DEA12/d/Arduino.app/Contents/Java/hardware/arduino/avr/variants/eightanaloginputs /var/folders/y8/0kkt82m53ys2jryw13_s1tgw0000gn/T/arduino_build_541564/sketch/pan_tilt_mount_nano_code_tmc2208.ino.cpp -o /dev/null
Using cached library dependencies for file: /var/folders/y8/0kkt82m53ys2jryw13_s1tgw0000gn/T/arduino_build_541564/sketch/Iibrary.cpp
Using cached library dependencies for file: /var/folders/y8/0kkt82m53ys2jryw13_s1tgw0000gn/T/arduino_build_541564/sketch/panTiltMount.cpp
Alternatives for MultiStepper.h: [AccelStepper]
ResolveLibrary(MultiStepper.h)
  -> candidates: [AccelStepper]
Alternatives for Iibrary.h: [library]
ResolveLibrary(Iibrary.h)
  -> candidates: [library]
Alternatives for EEPROM.h: [EEPROM@2.0]
ResolveLibrary(EEPROM.h)
  -> candidates: [EEPROM@2.0]
Using cached library dependencies for file: /Users/benmatthews/Documents/Arduino/libraries/AccelStepper/AccelStepper.cpp
Using cached library dependencies for file: /Users/benmatthews/Documents/Arduino/libraries/AccelStepper/MultiStepper.cpp
Using cached library dependencies for file: /Users/benmatthews/Documents/Arduino/libraries/library/Iibrary.cpp
Generating function prototypes...
/private/var/folders/y8/0kkt82m53ys2jryw13_s1tgw0000gn/T/AppTranslocation/272F7157-364F-421C-AACB-7350368DEA12/d/Arduino.app/Contents/Java/hardware/tools/avr/bin/avr-g++ -c -g -Os -w -std=gnu++11 -fpermissive -fno-exceptions -ffunction-sections -fdata-sections -fno-threadsafe-statics -Wno-error=narrowing -flto -w -x c++ -E -CC -mmcu=atmega328p -DF_CPU=16000000L -DARDUINO=10819 -DARDUINO_AVR_NANO -DARDUINO_ARCH_AVR -I/private/var/folders/y8/0kkt82m53ys2jryw13_s1tgw0000gn/T/AppTranslocation/272F7157-364F-421C-AACB-7350368DEA12/d/Arduino.app/Contents/Java/hardware/arduino/avr/cores/arduino -I/private/var/folders/y8/0kkt82m53ys2jryw13_s1tgw0000gn/T/AppTranslocation/272F7157-364F-421C-AACB-7350368DEA12/d/Arduino.app/Contents/Java/hardware/arduino/avr/variants/eightanaloginputs -I/Users/benmatthews/Documents/Arduino/libraries/AccelStepper -I/Users/benmatthews/Documents/Arduino/libraries/library -I/private/var/folders/y8/0kkt82m53ys2jryw13_s1tgw0000gn/T/AppTranslocation/272F7157-364F-421C-AACB-7350368DEA12/d/Arduino.app/Contents/Java/hardware/arduino/avr/libraries/EEPROM/src /var/folders/y8/0kkt82m53ys2jryw13_s1tgw0000gn/T/arduino_build_541564/sketch/pan_tilt_mount_nano_code_tmc2208.ino.cpp -o /var/folders/y8/0kkt82m53ys2jryw13_s1tgw0000gn/T/arduino_build_541564/preproc/ctags_target_for_gcc_minus_e.cpp
/private/var/folders/y8/0kkt82m53ys2jryw13_s1tgw0000gn/T/AppTranslocation/272F7157-364F-421C-AACB-7350368DEA12/d/Arduino.app/Contents/Java/tools-builder/ctags/5.8-arduino11/ctags -u --language-force=c++ -f - --c++-kinds=svpf --fields=KSTtzns --line-directives /var/folders/y8/0kkt82m53ys2jryw13_s1tgw0000gn/T/arduino_build_541564/preproc/ctags_target_for_gcc_minus_e.cpp
Compiling sketch...
/private/var/folders/y8/0kkt82m53ys2jryw13_s1tgw0000gn/T/AppTranslocation/272F7157-364F-421C-AACB-7350368DEA12/d/Arduino.app/Contents/Java/hardware/tools/avr/bin/avr-g++ -c -g -Os -w -std=gnu++11 -fpermissive -fno-exceptions -ffunction-sections -fdata-sections -fno-threadsafe-statics -Wno-error=narrowing -MMD -flto -mmcu=atmega328p -DF_CPU=16000000L -DARDUINO=10819 -DARDUINO_AVR_NANO -DARDUINO_ARCH_AVR -I/private/var/folders/y8/0kkt82m53ys2jryw13_s1tgw0000gn/T/AppTranslocation/272F7157-364F-421C-AACB-7350368DEA12/d/Arduino.app/Contents/Java/hardware/arduino/avr/cores/arduino -I/private/var/folders/y8/0kkt82m53ys2jryw13_s1tgw0000gn/T/AppTranslocation/272F7157-364F-421C-AACB-7350368DEA12/d/Arduino.app/Contents/Java/hardware/arduino/avr/variants/eightanaloginputs -I/Users/benmatthews/Documents/Arduino/libraries/AccelStepper -I/Users/benmatthews/Documents/Arduino/libraries/library -I/private/var/folders/y8/0kkt82m53ys2jryw13_s1tgw0000gn/T/AppTranslocation/272F7157-364F-421C-AACB-7350368DEA12/d/Arduino.app/Contents/Java/hardware/arduino/avr/libraries/EEPROM/src /var/folders/y8/0kkt82m53ys2jryw13_s1tgw0000gn/T/arduino_build_541564/sketch/pan_tilt_mount_nano_code_tmc2208.ino.cpp -o /var/folders/y8/0kkt82m53ys2jryw13_s1tgw0000gn/T/arduino_build_541564/sketch/pan_tilt_mount_nano_code_tmc2208.ino.cpp.o
Using previously compiled file: /var/folders/y8/0kkt82m53ys2jryw13_s1tgw0000gn/T/arduino_build_541564/sketch/Iibrary.cpp.o
Using previously compiled file: /var/folders/y8/0kkt82m53ys2jryw13_s1tgw0000gn/T/arduino_build_541564/sketch/panTiltMount.cpp.o
Compiling libraries...
Compiling library "AccelStepper"
Using previously compiled file: /var/folders/y8/0kkt82m53ys2jryw13_s1tgw0000gn/T/arduino_build_541564/libraries/AccelStepper/AccelStepper.cpp.o
Using previously compiled file: /var/folders/y8/0kkt82m53ys2jryw13_s1tgw0000gn/T/arduino_build_541564/libraries/AccelStepper/MultiStepper.cpp.o
Compiling library "library"
Using previously compiled file: /var/folders/y8/0kkt82m53ys2jryw13_s1tgw0000gn/T/arduino_build_541564/libraries/library/Iibrary.cpp.o
Compiling library "EEPROM"
Compiling core...
Using previously compiled file: /var/folders/y8/0kkt82m53ys2jryw13_s1tgw0000gn/T/arduino_build_541564/core/wiring_pulse.S.o
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
cbradburne, 2022-03-25:
Strange. I'm using Arduino IDE 1.8.19, macOS 12.3, selected board "Arduino Nano, ATmega328P, tried both boot loaders.
Compiles fine, with this result:

"Sketch uses 30388 bytes (98%) of program storage space. Maximum is 30720 bytes.
Global variables use 1503 bytes (73%) of dynamic memory, leaving 545 bytes for local variables. Maximum is 2048 bytes."

Did you put Isaac's "library" folder in to the Arduino/libraries folder? from here [LINK](https://github.com/isaac879/Iibrary)

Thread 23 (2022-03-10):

Loop

Nikitore, 2022-03-10:
I can't get it to work. I am sending the commands through the serial port of the Arduino Nano but the motors keep looping back and forth. Do you know why this is happening? I send a video where you can see the problem.

Nikitore, 2022-03-10:
Video

https://drive.google.com/file/d/13yk88zgiTplqRZulqzlmxvYA5bjrUprQ/view?usp=drivesdk

jkowalk, 2022-03-11:
Hi,
A quick google search helped me find these tips:
- Check if Speed is too high
- Check wiring (you might need to swap two wires; check out [this guide](https://buildbotics.com/wiring-stepper-motors/))
- Correctly adjust the potentiometer of the motor driver ([maybe this helps](https://all3dp.com/2/vref-calculator-tmc2209-tmc2208-a4988/))

Hope it helps...

Nikitore, 2022-03-11:
Thanks man! I'll check it out and let you know if it works.

Nikitore, 2022-03-23:
Hi! @jkowalk I checked the wiring and that was it. It was connected wrong. Thanks for your help.

Closed 2022-03-23.

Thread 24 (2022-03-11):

PORTB' was not declared in this scope

cinehorse, 2022-03-11:
I get this failure

In file included from sketch\panTiltMount.cpp:11:
C:\Program Files (x86)\Arduino\libraries\Bridge\src/YunClient.h:24:2: warning: #warning "The use of YunClient is deprecated. Use BridgeClient instead!" [-Wcpp]
 #warning "The use of YunClient is deprecated. Use BridgeClient instead!"
  ^~~~~~~
In file included from sketch\panTiltMount.cpp:12:
C:\Program Files (x86)\Arduino\libraries\Bridge\src/YunServer.h:24:2: warning: #warning "The use of YunServer is deprecated. Use BridgeServer instead!" [-Wcpp]
 #warning "The use of YunServer is deprecated. Use BridgeServer instead!"
  ^~~~~~~

sketch\panTiltMount.cpp: In function 'void setStepMode(int)':
panTiltMount.cpp:144:9: error: 'PORTB' was not declared in this scope

         PORTB |=   B00001000; //MS1 high

         ^~~~~

panTiltMount.cpp:148:9: error: 'PORTB' was not declared in this scope

         PORTB |=   B00000100; //MS2 high

         ^~~~~

panTiltMount.cpp:152:9: error: 'PORTB' was not declared in this scope

         PORTB &= ~(B00001100); //MS1 and MS2 low

         ^~~~~

panTiltMount.cpp:155:9: error: 'PORTB' was not declared in this scope

         PORTB |= B00001100; //MS1 and MS2 high

         ^~~~~

sketch\panTiltMount.cpp: In function 'int setTargetPositions(float, float, float)':

sketch\panTiltMount.cpp:291:1: warning: no return statement in function returning non-void [-Wreturn-type]

 }

 ^

exit status 1

'PORTB' was not declared in this scope   /* <--- was is PORTB for a declaration?

cbradburne, 2022-03-25:
Are you sure you've selected the Arduino Nano as the board?

From the error "The use of YunClient..." it looks like you've got the Arduino Yun selected instead.

I've just downloaded the current build, added the library files to the Arduino library folder, selected the Arduino Nano, and it compiled first time.

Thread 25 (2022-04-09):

The slider doesn't change direction when I tell it to.

Nikitore, 2022-04-09:
Hi, as I show in the video, when I try to change the direction of movement of the slider with the function ¨j¨ this does not change and continues in the same direction.

https://user-images.githubusercontent.com/99223586/162585901-b715d1ce-508c-41ad-9c05-24d15e7a3f28.mp4

I have already tested the wiring of the motors, changed the TCM 2208 driver, the continuity of the board between the output 3 of the arduino and the input inv of the driver. Everything indicates that this would be fine. But the problem continues, I am inclined to think that the Arduino is not sending the electric pulse to the driver to change direction.

Do you have any idea what it could be?

Translated with www.DeepL.com/Translator (free version)

isaac879, 2022-04-11:
The Arduino or TMC2208 might have a damaged/not working pin. I'd try replacing the Arduino and motor driver and see if either of them fixes the problem.
Does the slider move in the opposite direction if you enter a negative value?

Nikitore, 2022-04-11:
If I set negative values it keeps moving in the same direction. I tried swapping the stepper motor drivers and they all work correctly with the pan and tilt motors, but none of them work with the slider. So I was inclined to think that it might be the Arduino pin is damaged. I will try with another Arduino and let you know how it went.

Nikitore, 2022-04-15:
Hi, I have already changed the Arduino and now the slider axis is working, but unfortunately the pan and tilt axes stopped working. What should be the ideal Vref in the drivers? I have the following motor models. Pan and Tilt Usongshine US-17HS4023 and Slider KS 2sth40-1204a. In all 3 cases the Vref is set at 0.92 volts. Could this voltage be affecting the correct operation of the motors?

Nikitore, 2022-04-15:
And I think there must be some short circuit because both pan and tilt motors only being connected drained the battery very fast and overheated.

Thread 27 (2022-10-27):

3D printed bearing balls?

anrveira, 2022-10-27:
Hi, great job, thanks!

I can't find what diameter is needed for the balls used in the 3D printed bearing. Where did you get them?

Thanks.

isaac879, 2022-10-27:
Thank you!
I used 6mm BB pellets. You should be able to get them from many online sites or possibly in your local stores. I'd avoid super cheap, poor quality ones because they often have defects that make them not round...

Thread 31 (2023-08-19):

Printable bearing

gajjer, 2023-08-19:
I'm having trouble getting the printable bearing to fit. Using a vernier I think it is about 1mm larger when the parts are loaded with ball bearings. The outer ring split is about 3mm gap. Any suggestions?

ElektroMicha, 2024-01-14:
I printed the inner part of the bearing at 99.5%. This way I could make it fit properly. I think I even could try printing it at 99.7%, so I won't hear es much noise of the steel balls I'm using, since 99.5% is slightly too small.

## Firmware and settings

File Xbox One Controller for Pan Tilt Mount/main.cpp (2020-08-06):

/*------------------------------------------------------------------------------------------------------------------------------------------------------*/
/*
* THE SOFTWARE IS PROVIDED "AS IS", WITHOUT WARRANTY OF ANY KIND, EXPRESS OR IMPLIED, INCLUDING BUT NOT LIMITED TO THE WARRANTIES OF MERCHANTABILITY,
* FITNESS FOR A PARTICULAR PURPOSE AND NONINFRINGEMENT. IN NO EVENT SHALL THE AUTHORS OR COPYRIGHT HOLDERS BE LIABLE FOR ANY CLAIM, DAMAGES OR OTHER
* LIABILITY, WHETHER IN AN ACTION OF CONTRACT, TORT OR OTHERWISE, ARISING FROM, OUT OF OR IN CONNECTION WITH THE SOFTWARE OR THE USE OR OTHER DEALINGS
* IN THE SOFTWARE
*
* Code written by isaac879
*/
/*------------------------------------------------------------------------------------------------------------------------------------------------------*/

#include <stdio.h>
#include <Windows.h>
#include <Xinput.h>
#include <iostream>
#include <string>
#include <fstream>

/*------------------------------------------------------------------------------------------------------------------------------------------------------*/

//#pragma comment(lib, "XInput.lib")   // Library. If your compiler doesn't support this type of lib include change to the corresponding one

#define UP_BUTTON 1
#define DOWN_BUTTON 2
#define LEFT_BUTTON 4
#define RIGHT_BUTTON 8
#define MENU_BUTTON 16
#define VIEW_BUTTON 32
#define L_BUTTON 64
#define R_BUTTON 128
#define LB_BUTTON 256
#define RB_BUTTON 512
#define A_BUTTON 4096
#define B_BUTTON 8192
#define X_BUTTON 16384
#define Y_BUTTON 32768

#define INSTRUCTION_BYTES_PAN_SPEED 1
#define INSTRUCTION_BYTES_TILT_SPEED 2
#define INSTRUCTION_BYTES_PAN_TILT_SPEED 3
#define INSTRUCTION_BYTES_SLIDER_PAN_TILT_SPEED 4

#define INPUT_DEADZONE 4000

#define MAXIMUM_PAN_STEP_SPEED 1130.0 //steps per second
#define MAXIMUM_TILT_STEP_SPEED 410.0
#define MAXIMUM_SLIDER_STEP_SPEED 900.0

//triggers are 8 bit
//analogsticks are 16bit

//Flags
bool portOpenFlag = false; //The flag used to determin if the serial port for the Arduino Nano is opened
HANDLE hSerial;// Serial handle

/*------------------------------------------------------------------------------------------------------------------------------------------------------*/

byte getBytesFromInt(short sourceInt, unsigned int byteNumber) {//Gets a byte from an int. byte number should be 0 for the 8 least signigicant bits or 1 for the most fignificant bits
	byte byteValue = (sourceInt >> (8 * byteNumber)) & 0xFF;
	return byteValue;
}

/*------------------------------------------------------------------------------------------------------------------------------------------------------*/

void openSerial(LPCSTR port){
	if (portOpenFlag == false){//If the port is not already open
		hSerial = CreateFile(port, GENERIC_READ | GENERIC_WRITE, 0, NULL, OPEN_EXISTING, FILE_ATTRIBUTE_NORMAL, NULL);//Set the Com port to the correct arduino one

		if (hSerial == INVALID_HANDLE_VALUE){
			std::cout << "Error: invalid com port handle. Attempted to open: " << port << std::endl;
		}
		else{
			portOpenFlag = true;
			std::cout << "Successfully opened: " << port << std::endl;
		}
	}
}

/*------------------------------------------------------------------------------------------------------------------------------------------------------*/

int closeSerial(){
	if (portOpenFlag == true){//If the port is open
		if (CloseHandle(hSerial) == 0){
			std::cout << "Error\n" << stderr << std::endl;
			return -1;
		}
		portOpenFlag = false;
		printf("Serial port closed...\n");
		return 1;
	}
	return 0;
}

/*------------------------------------------------------------------------------------------------------------------------------------------------------*/

int serialConnect(LPCSTR portName){
	std::cout << "Attempting to open serial port " << portName << std::endl;
	openSerial(portName);//Open the serial port

	// Declare variables and structures
	DCB dcbSerialParams = { 0 };
	dcbSerialParams.DCBlength = sizeof(dcbSerialParams);//why do i need this?
	if (GetCommState(hSerial, &dcbSerialParams) == 0){
		closeSerial();
		return -1;
	}
	else{
		dcbSerialParams.BaudRate = CBR_57600; //Set device parameters (57600 baud, 1 start bit, 1 stop bit, no parity)
		dcbSerialParams.ByteSize = 8;
		dcbSerialParams.StopBits = ONESTOPBIT;
		dcbSerialParams.Parity = NOPARITY;
		dcbSerialParams.fDtrControl = DTR_CONTROL_DISABLE; //Stops the Arduino resetting after connecting
	}

	if(SetCommState(hSerial, &dcbSerialParams) == 0){
		closeSerial();
		return -1;
	}

	// Set COM port timeout settings
	COMMTIMEOUTS timeouts = { 0 };
	timeouts.ReadIntervalTimeout = 50;
	timeouts.ReadTotalTimeoutConstant = 50;
	timeouts.ReadTotalTimeoutMultiplier = 10;
	timeouts.WriteTotalTimeoutConstant = 50;
	timeouts.WriteTotalTimeoutMultiplier = 10;

	if(SetCommTimeouts(hSerial, &timeouts) == 0){
		closeSerial();
		return 1;
	}
	return 0;
}

/*------------------------------------------------------------------------------------------------------------------------------------------------------*/

int serialWrite(char data[], int lengthOfArray){
	DWORD bytes_written;
	if (!WriteFile(hSerial, data, lengthOfArray, &bytes_written, NULL)) {
		closeSerial();
		return -1;
	}
	return 0;
}

/*------------------------------------------------------------------------------------------------------------------------------------------------------*/

void printIncomingData(void){
	COMSTAT status;
	DWORD errors;
	DWORD bytesRead;//Number of bytes that have been read

	while(1){
		ClearCommError(hSerial, &errors, &status); //Use the ClearCommError function to get status info on the Serial port	
		if(status.cbInQue == 0) break;

		char* dataBuffer = new char[status.cbInQue + 1]; //buffer the size of the data available to be read
		dataBuffer[status.cbInQue] = '\0'; //adds a null terminator to the end of the buffer

		if(ReadFile(hSerial, dataBuffer, status.cbInQue, &bytesRead, NULL)){ //Try to read the require number of chars, and return the number of read bytes on success
			std::cout << dataBuffer;// << std::endl;
		}
		delete[] dataBuffer;
		Sleep(5); //Wait for 2ms before checking if more data has come in
	} 
}

/*------------------------------------------------------------------------------------------------------------------------------------------------------*/

void sendCommand(char command){
	char data[] = {command}; //Data array to send
	serialWrite(data, sizeof(data));
}

/*------------------------------------------------------------------------------------------------------------------------------------------------------*/

void sendCharArray(char *array){
	serialWrite(array, (int)strlen(array));
}

/*------------------------------------------------------------------------------------------------------------------------------------------------------*/

int sendStepSpeed(int command, short num){
	char data[3]; //Data array to send

	data[0] = command;
	data[1] = getBytesFromInt(num, 1);//Gets the 8 MSBs
	data[2] = getBytesFromInt(num, 0);//Gets the 8 LSBs

	serialWrite(data, sizeof(data)); //Send the command and the 4 bytes of data

	return 0;
}

/*------------------------------------------------------------------------------------------------------------------------------------------------------*/

int sendPanTiltStepSpeed(int command, int num){
	char data[5]; //Data array to send

	data[0] = command;
	data[1] = (num >> (8 * 3)) & 0xFF; //Gets the most significant byte
	data[2] = (num >> (8 * 2)) & 0xFF; //Gets the second most significant byte
	data[3] = (num >> (8 * 1)) & 0xFF; //Gets the third most significant byte
	data[4] = num & 0xFF; //Gets the least significant byte

	serialWrite(data, sizeof(data)); //Send the command and the 4 bytes of data

	return 0;
}

/*------------------------------------------------------------------------------------------------------------------------------------------------------*/

int sendSliderPanTiltStepSpeed(int command, short *arr){
	char data[7]; //Data array to send

	data[0] = command;
	data[1] = (arr[0] >> 8) & 0xFF; //Gets the most significant byte
	data[2] = arr[0] & 0xFF; //Gets the second most significant byte
	data[3] = (arr[1] >> 8) & 0xFF; 
	data[4] = arr[1] & 0xFF; 
	data[5] = (arr[2] >> 8) & 0xFF; 
	data[6] = arr[2] & 0xFF; //Gets the least significant byte

	serialWrite(data, sizeof(data)); //Send the command and the 6 bytes of data

	return 0;
}

/*------------------------------------------------------------------------------------------------------------------------------------------------------*/

std::string getPortName(std::string filePath){
	std::string line;
	std::cout << "Reading port name from: " << filePath << std::endl;
	std::ifstream readfile(filePath);

	if(readfile.is_open()){
		if (getline(readfile, line)){
			std::cout << "Port read from the file: " << line << std::endl;
		}
		readfile.close();
	}
	else {
		std::cout << "Error: Unable to open serial_port.txt" << std::endl;
	}
	return line;
}

/*------------------------------------------------------------------------------------------------------------------------------------------------------*/

int panTiltInit(void){
	//Connects to the com port that the Arduino is connected to.
	for(int i = 0; (i < 5) && (serialConnect(getPortName("D:\\Documents\\Projects\\Pan Tilt Mount\\serial_port.txt").c_str()) != 0 ); i++){ //path to .txt files containing the name of the COM port. The file should contain "\\.\COM10" without quotes to connect to COM10
		Sleep(1000);
		if(i == 4){
			std::cout << "Error: Unable to open serial port after 5 attempts..." << std::endl;
			return -1;
		}
	}
	return 0;
}

/*------------------------------------------------------------------------------------------------------------------------------------------------------*/

int main(void){
	panTiltInit();
	short shortVals[3] = {0, 0, 0};
	DWORD dwResult;   
	WORD lastwButtons = 0;
	DWORD lastDwPacketNumber = 0;
	for(DWORD i = 0; i < XUSER_MAX_COUNT; i++){
		XINPUT_STATE state;
		ZeroMemory(&state, sizeof(XINPUT_STATE));
	
		dwResult = XInputGetState(i, &state); //Simply get the state of the controller from XInput.
		if(dwResult == ERROR_SUCCESS){ //Controller is connected 
			printf("Connected.\n");
			while(1){
				if (GetKeyState(VK_ESCAPE) & 0x8000) { //MSB is key state (1 if pressed). LSB is the toggle state
					break;
				}
				if (GetKeyState(VK_F8) & 0x8000) {
					char data[10];
					std::cin.getline(data, 10);
					std::cin.clear();
					serialWrite(data, sizeof(data));
				}
				printIncomingData();
				XInputGetState(i, &state);
				//printf("dw packet number: %d\n", state.dwPacketNumber);
				if(state.dwPacketNumber != lastDwPacketNumber){
					short RXShort = 0;
					short RYShort = 0;
					short LXShort = 0;
					float RX = state.Gamepad.sThumbRX; //Get right analog stick X value
					float RY = state.Gamepad.sThumbRY; //Get right analog stick Y value
					float LX = state.Gamepad.sThumbLX; //Get left analog stick X value
					float LY = state.Gamepad.sThumbLY; //Get left analog stick Y value
					float magnitude = sqrt(RX * RX + RY * RY);
					float magnitudeL = sqrt(LX * LX + LY * LY);

					float normalizedMagnitude = 0;
					
					if(magnitude > INPUT_DEADZONE){ //check if the controller is outside a circular dead zone
						if(magnitude > 32767){ //clip the magnitude at its expected maximum value
							magnitude = 32767;
						}

						normalizedMagnitude = magnitude / (32767 - INPUT_DEADZONE);
						float scale = normalizedMagnitude / magnitude;
						RXShort = -((RX * scale) * abs(RX * scale) * MAXIMUM_PAN_STEP_SPEED);
						RYShort = -((RY * scale) * abs(RY * scale) * MAXIMUM_TILT_STEP_SPEED);
					}
					else{
						RXShort = 0;
						RYShort = 0;
					}

					float normalizedMagnitudeL = 0;
					if(magnitudeL > INPUT_DEADZONE){ //check if the controller is outside a circular dead zone
						if(magnitudeL > 32767){ //clip the magnitude at its expected maximum value
							magnitudeL = 32767;
						}

						normalizedMagnitudeL = magnitudeL / (32767 - INPUT_DEADZONE);
						float scale = normalizedMagnitudeL / magnitudeL;
						LXShort = (LX * scale) * abs(LX * scale) * MAXIMUM_SLIDER_STEP_SPEED;
					}
					else{
						LXShort = 0;
					}

					shortVals[0] = LXShort;
					printf("LXShort: %d \n", LXShort);
					shortVals[1] = RXShort;
					printf("RXShort: %d \n", RXShort);
					shortVals[2] = RYShort;
					printf("RYShort: %d \n", RYShort);

					sendSliderPanTiltStepSpeed(INSTRUCTION_BYTES_SLIDER_PAN_TILT_SPEED, shortVals); //send the combned values
					Sleep(10);

					if((lastwButtons & UP_BUTTON) < (state.Gamepad.wButtons & UP_BUTTON)){
						printf("Up: %d \n", (state.Gamepad.wButtons & UP_BUTTON));
						sendCharArray((char *)"@"); //Up first element
					}
					if((lastwButtons & DOWN_BUTTON) < (state.Gamepad.wButtons & DOWN_BUTTON)){
						printf("Down: %d \n", ((state.Gamepad.wButtons & UP_BUTTON) >> 1));
						sendCharArray((char *)"Z"); //down last element
					}
					if((lastwButtons & LEFT_BUTTON) < (state.Gamepad.wButtons & LEFT_BUTTON)){
						printf("Left: %d \n", ((state.Gamepad.wButtons & LEFT_BUTTON) >> 2));
						sendCharArray((char *)"<"); //left step back
					}
					if((lastwButtons & RIGHT_BUTTON) < (state.Gamepad.wButtons & RIGHT_BUTTON)){
						printf("Right: %d \n", ((state.Gamepad.wButtons & RIGHT_BUTTON) >> 3));
						sendCharArray((char *)">"); //right step forwards
					}
					if((lastwButtons & MENU_BUTTON) < (state.Gamepad.wButtons & MENU_BUTTON)){
						printf("Menu: %d \n", ((state.Gamepad.wButtons & MENU_BUTTON) >> 4));
						sendCharArray((char *)"A"); //Menu home
					}
					if((lastwButtons & VIEW_BUTTON) < (state.Gamepad.wButtons & VIEW_BUTTON)){
						printf("View: %d \n", ((state.Gamepad.wButtons & VIEW_BUTTON) >> 5));
						sendCharArray((char *)";1"); //views execute
					}
					if((lastwButtons & L_BUTTON) < (state.Gamepad.wButtons & L_BUTTON)){
						printf("L: %d \n", ((state.Gamepad.wButtons & L_BUTTON) >> 6));
						sendCharArray((char *)"m2"); //half step mode
					}
					if((lastwButtons & R_BUTTON) < (state.Gamepad.wButtons & R_BUTTON)){
						printf("R: %d \n", ((state.Gamepad.wButtons & R_BUTTON) >> 7));
						sendCharArray((char *)"m16"); //sixteenth step mode
					}
					if((lastwButtons & LB_BUTTON) < (state.Gamepad.wButtons & LB_BUTTON)){
						printf("LB: %d \n", ((state.Gamepad.wButtons & LB_BUTTON) >> 8));
						sendCharArray((char *)"D300"); //add delay of 300ms
					}
					if((lastwButtons & RB_BUTTON) < (state.Gamepad.wButtons & RB_BUTTON)){
						printf("RB: %d \n", ((state.Gamepad.wButtons & RB_BUTTON) >> 9));
						sendCharArray((char *)"c"); //RB Shutter
					}
					if((lastwButtons & A_BUTTON) < (state.Gamepad.wButtons & A_BUTTON)){
						printf("A: %d \n", ((state.Gamepad.wButtons & A_BUTTON) >> 12));
						sendCharArray((char *)"#"); //A save position
					}
					if((lastwButtons & B_BUTTON) < (state.Gamepad.wButtons & B_BUTTON)){
						printf("B: %d \n", ((state.Gamepad.wButtons & B_BUTTON) >> 13));
						sendCharArray((char *)"C"); //B clear array
					}
					if((lastwButtons & X_BUTTON) < (state.Gamepad.wButtons & X_BUTTON)){
						printf("X: %d \n", ((state.Gamepad.wButtons & X_BUTTON) >> 14));
						sendCharArray((char *)"E"); //X edit position
					}
					if((lastwButtons & Y_BUTTON) < (state.Gamepad.wButtons & Y_BUTTON)){
						printf("Y: %d \n", ((state.Gamepad.wButtons & Y_BUTTON) >> 15));
						sendCharArray((char *)"R"); //Y status
					}
					//printf("LX: %d \t", state.Gamepad.sThumbLX);
					//printf("LY: %d \t", state.Gamepad.sThumbLY);
					//printf("RX: %d \t", state.Gamepad.sThumbRX);
					//printf("RY: %d \n", state.Gamepad.sThumbRY);
					//printf("LT: %d \t", state.Gamepad.bLeftTrigger);
					//printf("RT: %d \n", state.Gamepad.bRightTrigger);
					//printf("wButtons %d \n", state.Gamepad.wButtons);
					lastwButtons = state.Gamepad.wButtons;
					lastDwPacketNumber = state.dwPacketNumber;
				}
			}
		}
		else{ //Controller is not connected 
			printf("Not Connected.\n");
		}
	}
	return 0;
}

/*------------------------------------------------------------------------------------------------------------------------------------------------------*/

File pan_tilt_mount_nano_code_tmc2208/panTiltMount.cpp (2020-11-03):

#include "PanTiltMount.h"
#include <Iibrary.h> //A library I created for Arduino that contains some simple functions I commonly use. Library available at: https://github.com/isaac879/Iibrary
#include <AccelStepper.h> //Library to control the stepper motors http://www.airspayce.com/mikem/arduino/AccelStepper/index.html
#include <MultiStepper.h> //Library to control multiple coordinated stepper motors http://www.airspayce.com/mikem/arduino/AccelStepper/classMultiStepper.html#details
#include <EEPROM.h> //To be able to save values when powered off

/*--------------------------------------------------------------------------------------------------------------------------------------------------------*/

//Global scope
AccelStepper stepper_pan = AccelStepper(1, PIN_STEP_PAN, PIN_DIRECTION_PAN);
AccelStepper stepper_tilt = AccelStepper(1, PIN_STEP_TILT, PIN_DIRECTION_TILT);
AccelStepper stepper_slider = AccelStepper(1, PIN_STEP_SLIDER, PIN_DIRECTION_SLIDER);

MultiStepper multi_stepper;

KeyframeElement keyframe_array[KEYFRAME_ARRAY_LENGTH];

int keyframe_elements = 0;
int current_keyframe_index = -1;
char stringText[MAX_STRING_LENGTH + 1];
float pan_steps_per_degree = (200.0 * SIXTEENTH_STEP * PAN_GEAR_RATIO) / 360.0; //Stepper motor has 200 steps per 360 degrees
float tilt_steps_per_degree = (200.0 * SIXTEENTH_STEP * TILT_GEAR_RATIO) / 360.0; //Stepper motor has 200 steps per 360 degrees
float slider_steps_per_millimetre = (200.0 * SIXTEENTH_STEP) / (SLIDER_PULLEY_TEETH * 2); //Stepper motor has 200 steps per 360 degrees, the timing pully has 36 teeth and the belt has a pitch of 2mm

int step_mode = SIXTEENTH_STEP;
bool enable_state = true; //Stepper motor driver enable state
float hall_pan_offset_degrees = 0; //Offset to make the pan axis home position centred. This is required because the Hall sensor triggers before being centred on the magnet.
float hall_tilt_offset_degrees = 0; //Offset to make the tilt axis home position centred. This is required because the Hall sensor triggers before being centred on the magnet.
byte invert_pan = 0; //Variables to invert the direction of the axis. Note: These value gets set from the saved EEPROM value on startup. 
byte invert_tilt = 0;
byte invert_slider = 0;
byte homing_mode = 0; //Note: Gets set from the saved EEPROM value on startup 
float pan_max_speed = 18; //degrees/second. Note: Gets set from the saved EEPROM value on startup. 
float tilt_max_speed = 10; //degrees/second.
float slider_max_speed = 20; //mm/second
long target_position[3]; //Array to store stepper motor step counts
float degrees_per_picture = 0.5; //Note: Gets set from the saved EEPROM value on startup. 
unsigned long delay_ms_between_pictures = 1000; //Note: Gets set from the saved EEPROM value on startup. 
int pan_accel_increment_us = 4000;
int tilt_accel_increment_us = 3000; 
int slider_accel_increment_us = 3500; 
byte acceleration_enable_state = 0;
FloatCoordinate intercept;

/*--------------------------------------------------------------------------------------------------------------------------------------------------------*/

void initPanTilt(void){
    Serial.begin(BAUD_RATE);
    pinMode(PIN_MS1, OUTPUT);
    pinMode(PIN_MS2, OUTPUT);
    pinMode(PIN_ENABLE, OUTPUT);
    pinMode(PIN_DIRECTION_PAN, OUTPUT);
    pinMode(PIN_STEP_PAN, OUTPUT);
    pinMode(PIN_DIRECTION_TILT, OUTPUT);
    pinMode(PIN_STEP_TILT, OUTPUT);
    pinMode(PIN_DIRECTION_SLIDER, OUTPUT);
    pinMode(PIN_STEP_SLIDER, OUTPUT);
    pinMode(PIN_PAN_HALL, INPUT_PULLUP);
    pinMode(PIN_TILT_HALL, INPUT_PULLUP);
    pinMode(PIN_SLIDER_HALL, INPUT_PULLUP);
    pinMode(PIN_SHUTTER_TRIGGER, OUTPUT);
    digitalWrite(PIN_SHUTTER_TRIGGER, LOW);
    setEEPROMVariables();
    setStepMode(step_mode); //steping mode
    stepper_pan.setMaxSpeed(panDegreesToSteps(pan_max_speed));
    stepper_tilt.setMaxSpeed(tiltDegreesToSteps(tilt_max_speed));
    stepper_slider.setMaxSpeed(sliderMillimetresToSteps(slider_max_speed));
    stepper_pan.setAcceleration(5000);
    stepper_tilt.setAcceleration(5000);
    stepper_slider.setAcceleration(5000);
    invertPanDirection(invert_pan);
    invertTiltDirection(invert_tilt);
    invertSliderDirection(invert_slider);
    multi_stepper.addStepper(stepper_pan);
    multi_stepper.addStepper(stepper_tilt);
    multi_stepper.addStepper(stepper_slider);
    digitalWrite(PIN_ENABLE, LOW); //Enable the stepper drivers
//    if(homing_mode == 1){
//        printi(F("Homing\n"));
//        if(findHome()){
//            printi(F("Complete\n"));
//        }
//        else{
//            stepper_pan.setCurrentPosition(0);
//            stepper_tilt.setCurrentPosition(0);
//            printi(F("Error homing\n"));
//        }
//    }
}

/*--------------------------------------------------------------------------------------------------------------------------------------------------------*/

float boundFloat(float value, float lower, float upper){
    if(value < lower){
        value = lower;
    }
    else if(value > upper){
        value = upper;
    }
    return value;
}

/*--------------------------------------------------------------------------------------------------------------------------------------------------------*/

void serialFlush(void){
    while(Serial.available() > 0){
        char c = Serial.read();
    }
} 

/*--------------------------------------------------------------------------------------------------------------------------------------------------------*/

void enableSteppers(void){
    if(enable_state == false){
        digitalWrite(PIN_ENABLE, LOW); //Enable the stepper drivers
        enable_state = true;
        printi(F("Enabled\n"));
    }
    else{
        digitalWrite(PIN_ENABLE, HIGH); //Disabe the stepper drivers
        enable_state = false;
        printi(F("Disabled\n"));
    }
}

/*--------------------------------------------------------------------------------------------------------------------------------------------------------*/
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

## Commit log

2020-07-15 Add files via upload
    Corrected a mistake listing two 15k resistors instead of a 15k and 22k resistor.
2020-07-21 Add files via upload
    Updated for use with the TMC2208 stepper drivers.
    Added some acceleration controls.
2020-08-17 Add files via upload
    Switched the pan and slider stepper driver pins.
2020-09-07 Add files via upload
    Corrected stepper motor quantities.
2020-10-24 Add files via upload
    STEP CAD files added
    [127 x 146.05 x 12.7mm Printable Bearing Cage Part 3.stp, 127 x 146.05 x 12.7mm Printable Bearing Part 1.stp, 127 x 146.05 x 12.7mm Printable Bearing Part 2.stp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]
2020-11-03 Add files via upload
    - Fixed bugs in the timelapse function.
    - Improved the step to mm conversion accuracy.
    - Battery is now given as a voltage not percentage.
    [panTiltMount.cpp, panTiltMount.h, pan_tilt_mount_nano_code_tmc2208.ino]
